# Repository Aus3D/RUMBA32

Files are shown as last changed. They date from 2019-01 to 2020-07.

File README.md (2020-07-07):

# RUMBA32




RUMBA32 is a 32-bit version of the RUMBA 3D Printer control board. RUMBA32 is derived from the Aus3D [RUMBA+](https://github.com/Aus3D/RUMBA-Plus) design, which is an overhauled version of the original RUMBA.

RUMBA32 combines the improved RUMBA+ design with a powerful 32-bit STM32F446 microcontroller.

In keeping with the original RUMBA design, RUMBA32 is fully open source. RUMBA32 boards are available for sale in the [Aus3D shop](https://aus3d.com.au/rumba32). 

Instructions for configuring and uploading Marlin using PlatformIO can be found on the [Marlin - Build and Upload (PlatformIO)](https://github.com/Aus3D/RUMBA32/wiki/Marlin---Build-and-Upload-(PlatformIO)) wiki page.

## Firmware Support
RUMBA32 is currently supported by the following firmware:
- [MK4duo (support in v4.4.0)](https://github.com/MKFirmware/MK4duo)
- [Marlin 2.0 (support in bugfix-2.0.x)](https://github.com/MarlinFirmware/Marlin)
- [Repetier-Firmware V2 (support in dev2)](https://github.com/repetier/Repetier-Firmware/tree/dev2)

## Images
### Overview
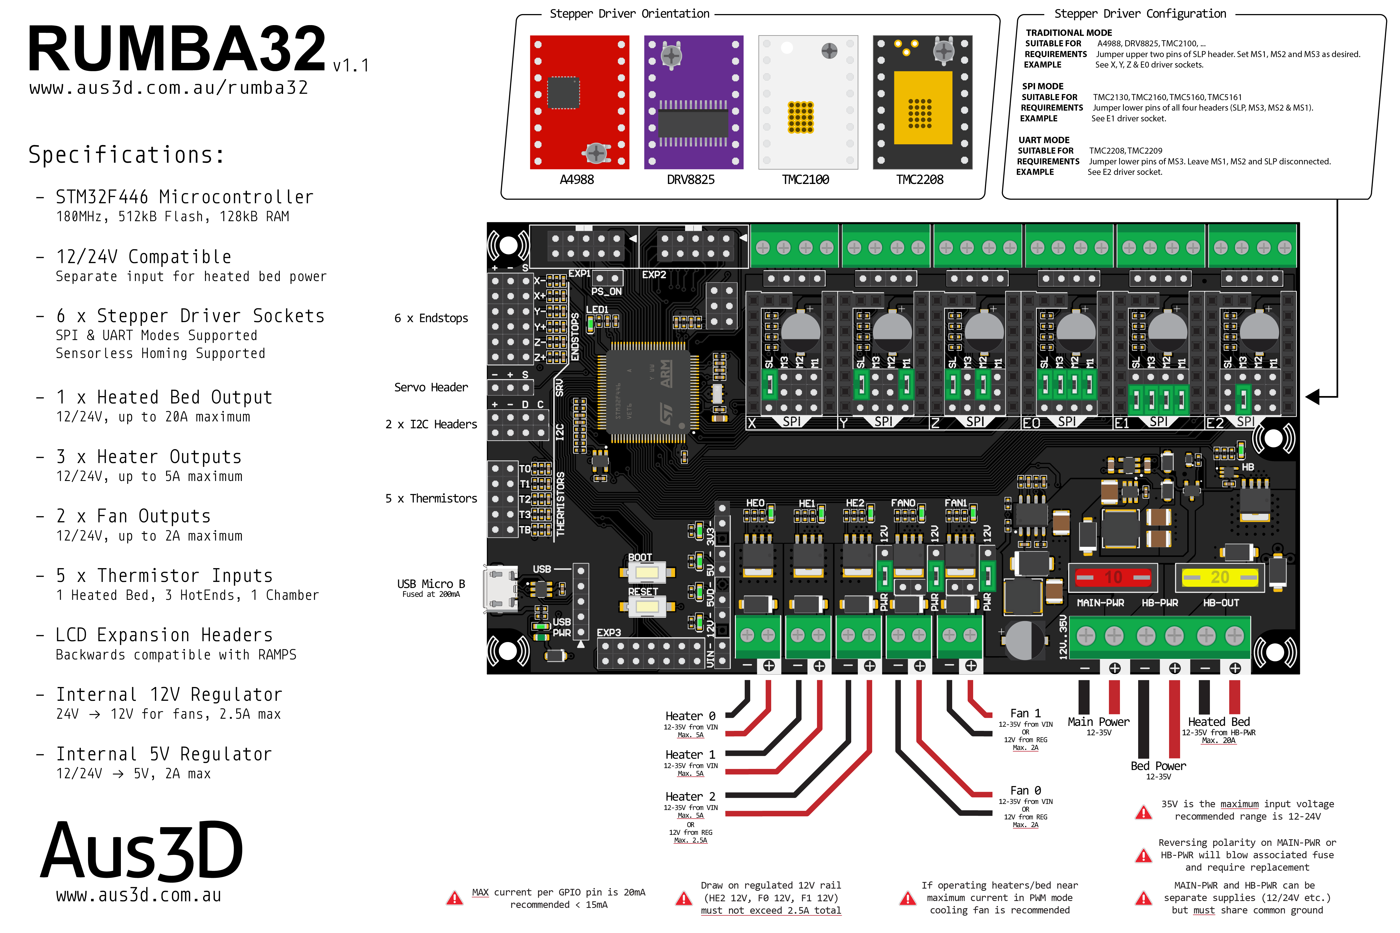
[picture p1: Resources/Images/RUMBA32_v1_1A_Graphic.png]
RUMBA32 Graphic

### Photo
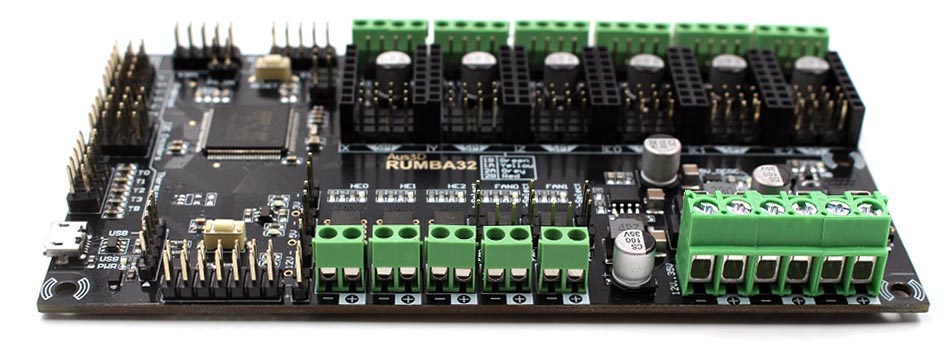
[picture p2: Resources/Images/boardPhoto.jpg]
RUMBA32 Photo

### Schematic
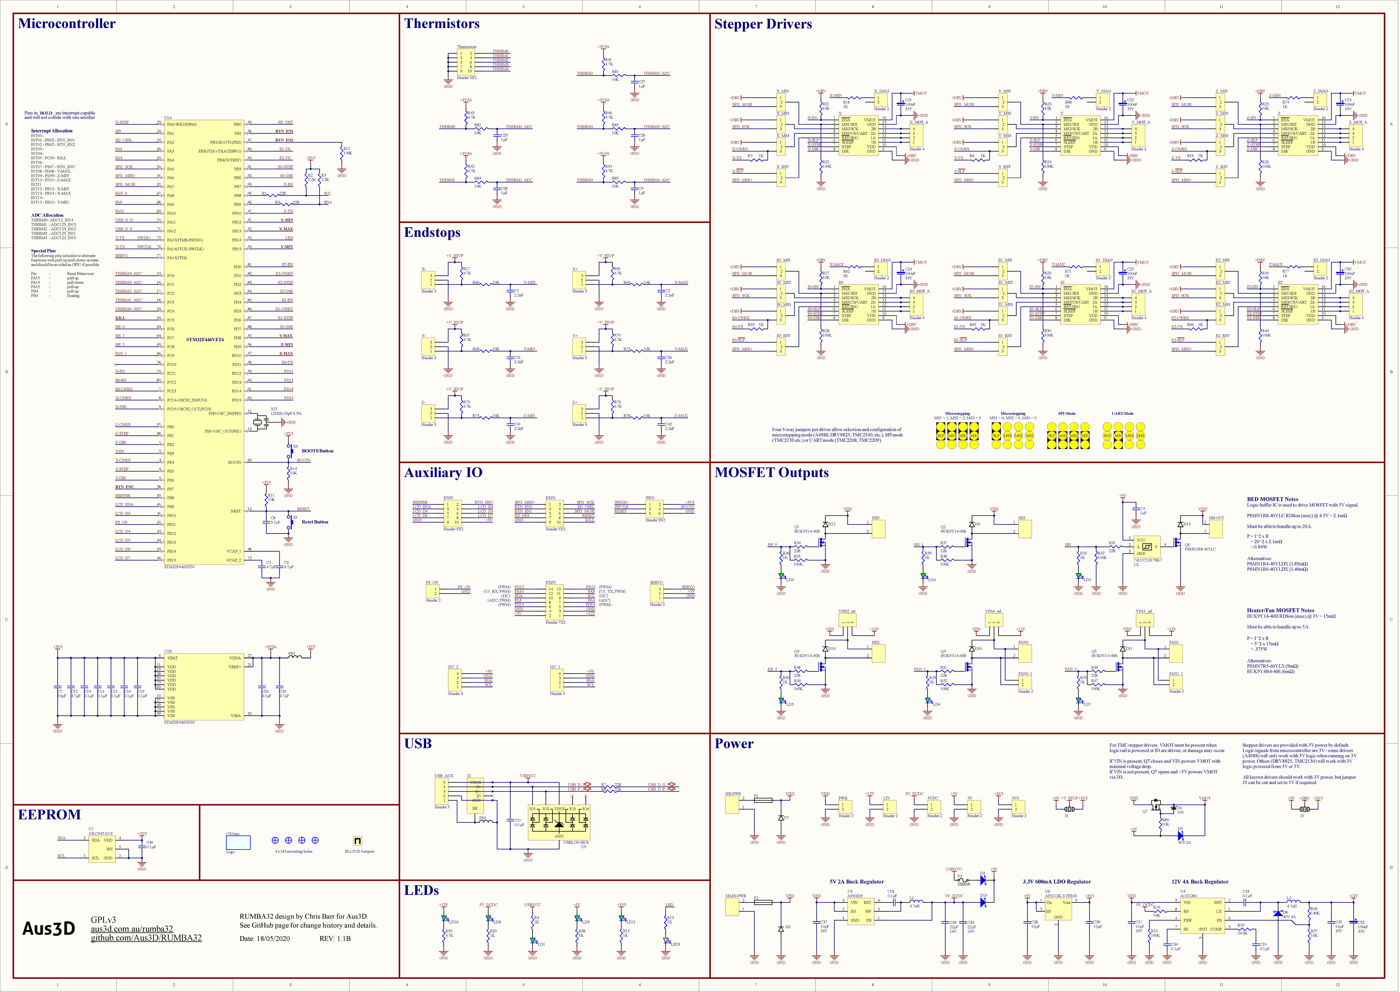
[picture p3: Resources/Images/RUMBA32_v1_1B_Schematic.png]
RUMBA32 Schematic

### Pinout
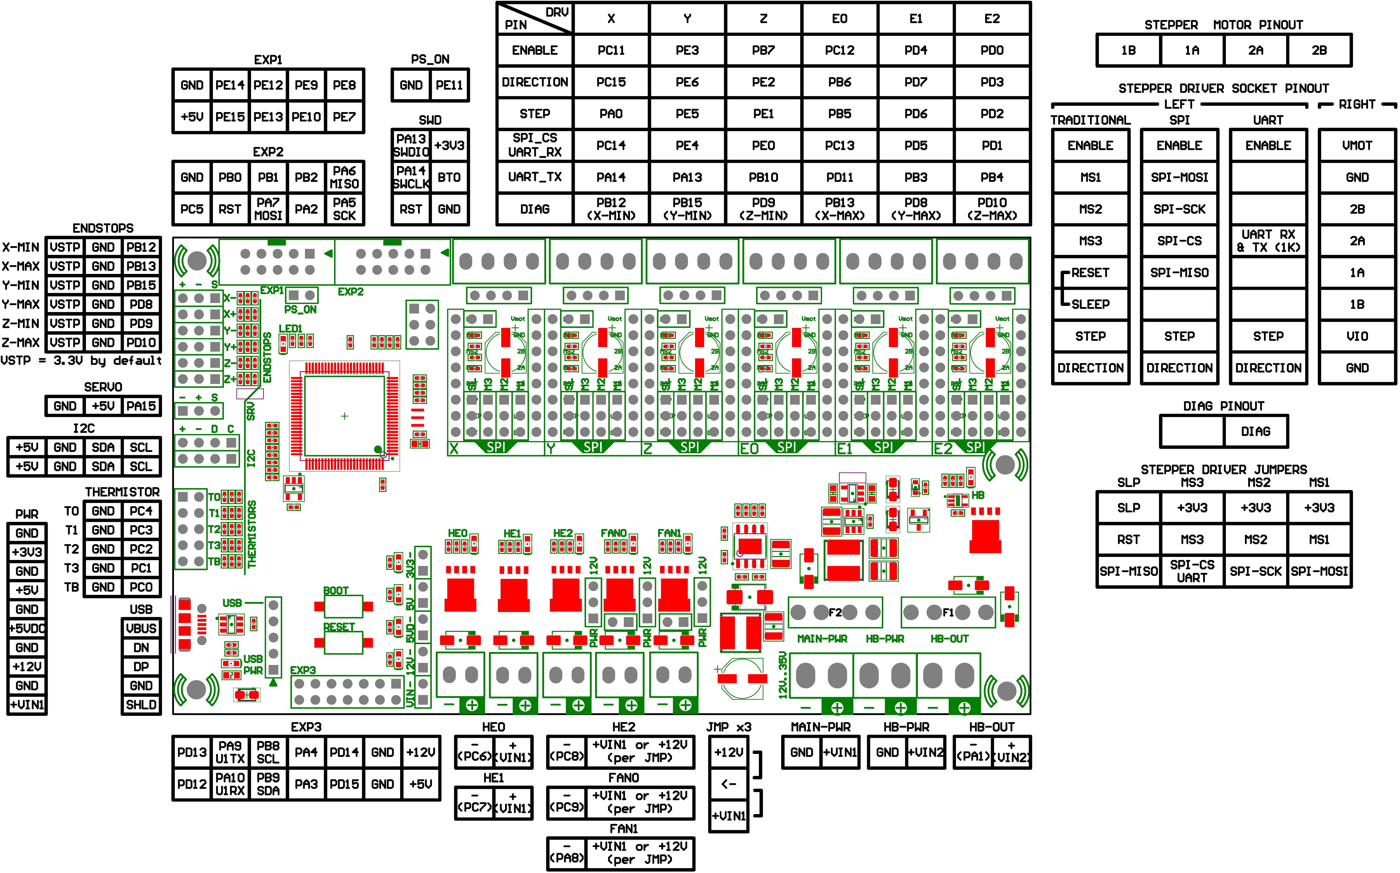
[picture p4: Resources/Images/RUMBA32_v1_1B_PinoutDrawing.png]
RUMBA32 Pinout

### Dimensions
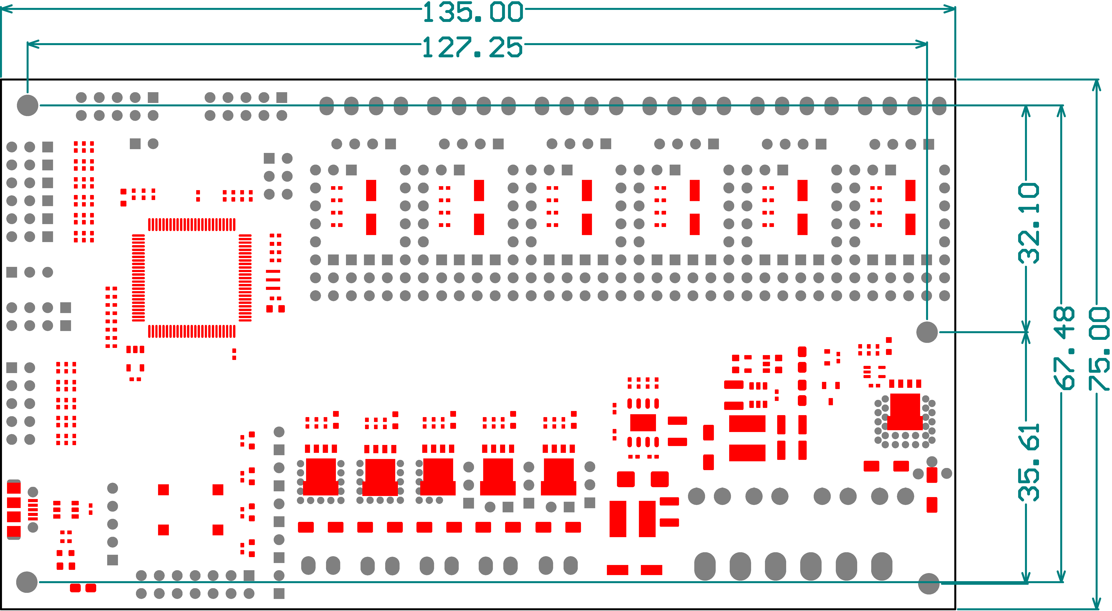
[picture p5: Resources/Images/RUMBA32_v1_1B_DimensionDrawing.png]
RUMBA32 Dimensions


## License
RUMBA32 is fully open source, and may be freely modified or changed by anyone, provided they maintain the license it is released under. The design is free to use for any purpose, including commercial uses. RUMBA32 maintains the GPLv2 license of the original RUMBA board. For more information on this license, please see the included license file.

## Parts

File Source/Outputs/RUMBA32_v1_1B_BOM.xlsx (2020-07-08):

Designator | Description | Quantity | Note | Manufacturer 1 | Manufacturer Part Number 1 | Supplier 1 | Supplier Part Number 1
JMP, JMP1 | 2.54mm .1" PCB Jumper, Green | 28 | Installed as per drawing, approved sub OK | Sullins | QPC02SXGN-RC | Digi-Key | S9337-ND
C21, C22, C23, C24, C25, C30, C32 | CAP ALUM 100UF 20% 35V SMD | 7 | Approved sub OK | Panasonic | EEEFT1V101AP | Digi-Key | PCE5016CT-ND
C8, C10, C11, C13, C14, C15, C16, C18, C19, C20, C33, C34, C40 | CAP CER 0.1UF 50V X7R 0402 | 13 | Approved sub OK | Taiyo Yuden | UMK105B7104KV-FR | Digi-Key | 587-3498-1-ND
C4, C9, C26, C27, C28, C29 | CAP CER 1UF 16V X5R 0402 | 6 | Approved sub OK | Taiyo | EMK105BJ105KV-F | Digi-Key | 587-2477-1-ND
C1, C2, C31, C36, C41, C42 | CAP CER 2.2NF 50V X7R 0402 | 6 | Approved sub OK | Taiyo Yuden | RMUMK105B7222KV-F | Digi-Key | 587-1221-1-ND
C5, C6, C12, C35 | CAP CER 4.7UF 10V X5R 0402 | 4 | Approved sub OK | Taiyo Yuden | LMK105BBJ475MVLF | Digi-Key | 587-3408-1-ND
C7, C38, C39 | CAP CER 10UF 10V X5R 0603 | 3 | Approved sub OK | Taiyo Yuden | LMK107BBJ106KALT | Digi-Key | 587-6017-1-ND
C17, C37, C45 | CAP CER 10UF 35V X7R 1210 | 3 | Approved sub OK | Taiyo Yuden | GMJ325KB7106KMHP | Digi-Key | 587-4890-1-ND
C43, C44 | CAP CER 22UF 16V X7R 1210 | 2 | Approved sub OK | Taiyo Yuden | EMJ325KB7226KMHP | Digi-Key | 587-5657-1-ND
XT1 | CER RES 12.0000MHZ 33PF SMD | 1 | Approved sub OK | Murata | CSTNE12M0G550000R0 | Digi-Key | 490-17943-1-ND
J2 | CONN RCPT USB2.0 MICRO B SMD R/A | 1 | Approved sub OK | Molex | 105017-0001 | Digi-Key | WM1399CT-ND
D6, D7, D9, D10, D11, D12, D13, D14 | DIODE GEN PURP 100V 1.5A SMA | 8 | Approved sub OK | Diodes | S2BA-13-F | Digi-Key | S2BA-FDICT-ND
D3, D4, D15 | DIODE SCHOTTKY 40V 2A SOD123F | 3 | Approved sub OK | ON Semiconductor / Fairchild | SS24FL | Digi-Key | SS24FLCT-ND
D8 | DIODE SCHOTTKY 40V 4A DO214AA | 1 | Approved sub OK | Vishay Semiconductors | SSB44-E3/52T | Digi-Key | SSB44-E3/52TGICT-ND
U5 | DIODE TVS 5.25V 17V SOT23-6 | 1 | Approved sub OK | STMicroelectronics | USBLC6-4SC6 | Digi-Key | 497-4492-1-ND
D1 | DIODE ZENER 10V 500mW SOD523 | 1 | Approved sub OK | ON Semiconductor | MM5Z10VT1G | Digi-Key | MM5Z10VT1GOSCT-ND
FB1, FB2 | FERRITE BEAD 120R 300MA 0402 | 2 | Approved sub OK | Taiyo Yuden | BK1005HM121-T | Digi-Key | 587-1836-1-ND
L1, L2 | FIXED IND 4.7UH 4.5A 26 MOHM SMD | 2 | Approved sub OK | Bourns | SRN6045TA-4R7M | Digi-Key | SRN6045TA-4R7MCT-ND
F1, F2 | FUSE HOLDER BLADE PCB | 2 | Approved sub OK | Memory Protection Devices | BK-6013 | Digi-Key | BK-6013-ND
3V3, 5V, 5VDC, 12V, FAN0_1, FAN1_1, PS_ON, PWR | Header, 2-Pin | 8 | Approved sub OK | Generic Header
E0_DIAG, E1_DIAG, E2_DIAG, X_DIAG, Y_DIAG, Z_DIAG | Header, 2-Pin, Female | 6 | Approved sub OK | Generic Header
E0_MS1, E0_MS2, E0_MS3, E0_RST, E1_MS1, E1_MS2, E1_MS3, E1_RST, E2_MS1, E2_MS2, E2_MS3, E2_RST, SERVO, VFA0_sel, VFA1_sel, VHE2_sel, X-, X_MS1, X_MS2, X_MS3, X_RST, X+, Y-, Y_MS1, Y_MS2, Y_MS3, Y_RST, Y+, Z-, Z_MS1, Z_MS2, Z_MS3, Z_RST, Z+ | Header, 3-Pin | 34 | Approved sub OK | Generic Header
SWD | Header, 3-Pin, Dual row | 1 | Approved sub OK | Generic Header
E0_MOT_A, E1_MOT_A, E2_MOT_A, I2C_1, I2C_2, X_MOT_A, Y_MOT_A, Z_MOT_A | Header, 4-Pin | 8 | Approved sub OK | Generic Header
USB_AUX | Header, 5-Pin | 1 | Approved sub OK | Generic Header
EXP1, EXP2, Thermistors | Header, 5-Pin, Dual row | 3 | Approved sub OK | Generic Header
EXP3 | Header, 7-Pin, Dual row | 1 | Approved sub OK | Generic Header
E0_0, E0_1, E1_0, E1_1, E2_0, E2_1, X_0, X_1, Y_0, Y_1, Z_0, Z_1 | Header, 8-Pin, Female | 12 | Approved sub OK | Generic Header
U2 | IC BUF NON-INVERT 5.5V SOT353 | 1 |  | Diodes | 74LVC1G17SE-7 | Digi-Key | 74LVC1G17SE-7CT-ND
U7 | IC EEPROM 64K I2C SOT23-5 | 1 |  | Microchip | 24LC64T-I/OT | Digi-Key | 24LC64T-I/OTCT-ND
U1 | IC MCU 32BIT 512KB FLASH 100LQFP | 1 |  | STMicroelectronics | STM32F446VET6 | Digi-Key | 497-15375-ND
U3 | IC REG BUCK 5V 2A SOT23-6 | 1 |  | Diodes | AP63205WU-7 | Digi-Key | AP63205WU-7DICT-ND
U4 | IC REG BUCK ADJ 4A 8SO | 1 |  | Alpha & Omega Semiconductor | AOZ1284PI | Digi-Key | 785-1689-1-ND
U6 | IC REG LINEAR 3.3V 600MA SOT25 | 1 |  | Diodes | AP2112K-3.3TRG1 | Digi-Key | AP2112K-3.3TRG1DICT-ND
LD1, LD2, LD3, LD4, LD5, LD6, LD7, LD8, LD9, LD10, LD11 | LED GREEN CLEAR CHIP SMD 0603 | 11 | Approved sub OK | Vishay Lite-On | LTST-C190KGKT | Digi-Key | 160-1435-2-ND
LED1 | LED YELLOW CLEAR CHIP SMD 0603 | 1 | Approved sub OK | Vishay Lite-On | LTST-C190KSKT | Digi-Key | 160-1437-1-ND
Q1, Q2, Q3, Q4, Q5 | MOSFET N-CH 40V 56A LFPAK | 5 |  | Nexperia USA | BUK9Y14-40B,115 | Digi-Key | 1727-4940-1-ND
Q6 | MOSFET N-CH 40V 100A LFPAK | 1 |  | Nexperia | PSMN1R8-40YLC,115 | Digi-Key | 1727-1052-1-ND
Q7 | MOSFET SMD P-CH 30V 4.8A SOT-23-3 | 1 |  | Vishay Siliconix | SI2371EDS-T1-GE3 | Digi-Key | SI2371EDS-T1-GE3CT-ND
F3 | PTC RESET FUSE 9V 200MA 0603 | 1 | Approved sub OK | BEL FUSE - CIRCUIT PROTECTION | 0ZCM0020FF2G | Digi-Key | 507-1821-1-ND
R4, R5, R6, R13, R15, R16, R18, R20, R33, R36, R39, R50, R53, R55, R58, R62, R64, R65, R66, R68, R71, R74, R77 | RES SMD 1K OHM 1% 1/16W 0402 | 23 | Approved sub OK | Yageo | RC0402FR-071KL | Digi-Key | 311-1.00KLRCT-ND
R2, R3 | RES SMD 2.2K OHM 1% 1/16W 0402 | 2 | Approved sub OK | Yageo | RC0402FR-072K2L | Digi-Key | 311-2.20KLRCT-ND
R17, R40, R41, R42, R43, R54, R59, R61, R67, R70, R73, R76 | RES SMD 4.7K OHM 1% 1/16W 0402 | 12 | Approved sub OK | Yageo | RC0402FR-074K7L | Digi-Key | 311-4.7KLRCT-ND
R11, R14, R21, R23, R25, R27, R29, R45, R57, R60, R63, R69, R72, R75, R78, R79, R80, R81, R82, R83, R84, R85 | RES SMD 10K OHM 1% 1/16W 0402 | 22 | Approved sub OK | Yageo | RC0402FR-0710KL | Digi-Key | 311-10.0KLRCT-ND
R1, R7, R8, R9, R31, R34, R37, R46, R48, R51 | RES SMD 22 OHM 1% 1/16W 0402 | 10 | Approved sub OK | Yageo | RC0402FR-0722RL | Digi-Key | 311-22.0LRCT-ND
R19 | RES SMD 54.9K OHM 1% 1/16W 0402 | 1 | Approved sub OK | Yageo | RC0402FR-0754K9L | Digi-Key | YAG3185CT-ND
R10, R12, R22, R24, R26, R28, R30, R32, R35, R38, R44, R47, R49, R52 | RES SMD 100K OHM 1% 1/16W 0402 | 14 | Approved sub OK | Yageo | RC0402FR-07100KL | Digi-Key | 311-100KLRCT-ND
R56 | RES SMD 140K OHM 1% 1/16W 0402 | 1 | Approved sub OK | Yageo | RC0402FR-07140KL | Digi-Key | YAG2978CT-ND
S1, S3 | SWITCH TACTILE SPST-NO 0.05A 12V | 2 | Approved sub OK | APEM | MJTP1106SATR | Digi-Key | 679-2396-1-ND
FAN0, FAN1, HE0, HE1, HE2 | TERM BLK 2POS SIDE ENT 3.5MM PCB | 5 | Approved sub OK | Phoenix Contact | 1751248 | Digi-Key | 277-5719-ND
HB-OUT, HB-PWR, MAIN-PWR | TERM BLK 2POS SIDE ENTRY 5MM PCB | 3 |  | Phoenix Contact | 1935776 | Digi-Key | 277-6405-ND
E0_MOT, E1_MOT, E2_MOT, X_MOT, Y_MOT, Z_MOT | TERM BLK 4POS SIDE ENT 3.5MM PCB | 6 | Approved sub OK | Phoenix Contact | 1751264 | Digi-Key | 277-5744-ND

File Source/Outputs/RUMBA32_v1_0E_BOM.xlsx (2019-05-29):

Designator | Description | Quantity | Note | Manufacturer 1 | Manufacturer Part Number 1 | Supplier 1 | Supplier Part Number 1
JMP | 2.54mm .1" PCB Jumper, Green | 27 | Installed as per drawing, approved sub OK | Sullins (https://octopart-clicks.com/click/altium?sku=S9337-ND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) | QPC02SXGN-RC (https://octopart-clicks.com/click/altium?sku=S9337-ND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) | Digi-Key | S9337-ND (https://octopart-clicks.com/click/altium?sku=S9337-ND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)
C1, C21, C22, C23, C24, C25, C30, C31, C32 | CAP ALUM 100UF 20% 35V SMD | 9 | Approved sub OK | Panasonic (https://octopart-clicks.com/click/altium?sku=PCE5016CT-ND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) | EEEFT1V101AP (https://octopart-clicks.com/click/altium?sku=PCE5016CT-ND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) | Digi-Key | PCE5016CT-ND (https://octopart-clicks.com/click/altium?sku=PCE5016CT-ND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)
C3, C8, C10, C11, C13, C14, C15, C16, C18, C19, C20, C33, C34 | CAP CER 0.1UF 50V X7R 0603 | 13 | Approved sub OK | Yageo (https://octopart-clicks.com/click/altium?sku=311-1344-1-ND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) | CC0603KRX7R9BB104 (https://octopart-clicks.com/click/altium?sku=311-1344-1-ND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) | Digi-Key | 311-1344-1-ND (https://octopart-clicks.com/click/altium?sku=311-1344-1-ND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)
C4, C9, C26, C27, C28, C29 | CAP CER 1UF 16V X7R 0603 | 6 | Approved sub OK | Taiyo Yuden (https://octopart-clicks.com/click/altium?sku=587-1241-1-ND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) | EMK107B7105KA-T (https://octopart-clicks.com/click/altium?sku=587-1241-1-ND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) | Digi-Key | 587-1241-1-ND (https://octopart-clicks.com/click/altium?sku=587-1241-1-ND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)
C2, C5, C6, C12, C35, C38, C39 | CAP CER 4.7UF 10V X7R 0603 | 7 | Approved sub OK | TDK (https://octopart-clicks.com/click/altium?sku=445-1604-1-ND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) | C1608X7R1C105K080AC (https://octopart-clicks.com/click/altium?sku=445-1604-1-ND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) | Digi-Key | 445-1604-1-ND (https://octopart-clicks.com/click/altium?sku=445-1604-1-ND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)
C17, C36, C37 | CAP CER 4.7UF 50V X7R 1210 | 3 | Approved sub OK | KEMET (https://octopart-clicks.com/click/altium?sku=399-6785-1-ND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) | C1210C475K5RACTU (https://octopart-clicks.com/click/altium?sku=399-6785-1-ND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) | Digi-Key | 399-6785-1-ND (https://octopart-clicks.com/click/altium?sku=399-6785-1-ND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)
C7 | CAP CER 10UF 6.3V X7R 0805 | 1 | Approved sub OK | Samsung (https://octopart-clicks.com/click/altium?sku=1276-1113-1-ND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) | CL21B106KQQNNNE (https://octopart-clicks.com/click/altium?sku=1276-1113-1-ND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) | Digi-Key | 1276-1113-1-ND (https://octopart-clicks.com/click/altium?sku=1276-1113-1-ND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)
XT1 | CER RES 12.0000MHZ 33PF SMD | 1 | Approved sub OK | Murata (https://octopart-clicks.com/click/altium?sku=490-17943-1-ND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) | CSTNE12M0G550000R0 (https://octopart-clicks.com/click/altium?sku=490-17943-1-ND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) | Digi-Key | 490-17943-1-ND (https://octopart-clicks.com/click/altium?sku=490-17943-1-ND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)
J2 | CONN RCPT USB2.0 MICRO B SMD R/A | 1 | Approved sub OK | Molex (https://octopart-clicks.com/click/altium?sku=WM1399CT-ND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) | 105017-0001 (https://octopart-clicks.com/click/altium?sku=WM1399CT-ND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) | Digi-Key | WM1399CT-ND (https://octopart-clicks.com/click/altium?sku=WM1399CT-ND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)
D6, D7, D9, D10, D11, D12, D13, D14 | DIODE GEN PURP 100V 1.5A SMA | 8 | Approved sub OK | Diodes (https://octopart-clicks.com/click/altium?sku=S2BA-FDICT-ND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) | S2BA-13-F (https://octopart-clicks.com/click/altium?sku=S2BA-FDICT-ND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) | Digi-Key | S2BA-FDICT-ND (https://octopart-clicks.com/click/altium?sku=S2BA-FDICT-ND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)
D3, D4, D5, D15 | DIODE SCHOTTKY 40V 2A SOD123F | 4 | Approved sub OK | ON Semiconductor / Fairchild (https://octopart-clicks.com/click/altium?manufacturer=ON%20Semiconductor%20%2F%20Fairchild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) | SS24FL (https://octopart-clicks.com/click/altium?manufacturer=ON%20Semiconductor%20%2F%20Fairchild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) | Digi-Key | SS24FLCT-ND (https://octopart-clicks.com/click/altium?manufacturer=ON%20Semiconductor%20%2F%20Fairchild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)
D2, D8 | DIODE SCHOTTKY 40V 4A DO214AA | 2 | Approved sub OK | General Instruments (https://octopart-clicks.com/click/altium?manufacturer=General%20Instruments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) | SSB44-E3/52T (https://octopart-clicks.com/click/altium?manufacturer=General%20Instruments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) | Digi-Key | SSB44-E3/52TGICT-ND (https://octopart-clicks.com/click/altium?manufacturer=General%20Instruments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)
FB1, FB2 | FERRITE BEAD 120 OHM 0603 1LN | 2 | Approved sub OK | Murata (https://octopart-clicks.com/click/altium?sku=490-1037-1-ND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) | BLM18PG-121SN1D (https://octopart-clicks.com/click/altium?sku=490-1037-1-ND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) | Digi-Key | 490-1037-1-ND (https://octopart-clicks.com/click/altium?sku=490-1037-1-ND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)
L2 | FIXED IND 4.7UH 4.5A 26 MOHM SMD | 1 | Approved sub OK | Bourns (https://octopart-clicks.com/click/altium?sku=SRN6045TA-4R7MCT-ND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) | SRN6045TA-4R7M (https://octopart-clicks.com/click/altium?sku=SRN6045TA-4R7MCT-ND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) | Digi-Key | SRN6045TA-4R7MCT-ND (https://octopart-clicks.com/click/altium?sku=SRN6045TA-4R7MCT-ND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)
L1 | FIXED IND 33UH 1.8A 145 MOHM SMD | 1 | Approved sub OK | Bourns (https://octopart-clicks.com/click/altium?sku=SRN6045TA-330MCT-ND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) | SRN6045TA-330M (https://octopart-clicks.com/click/altium?sku=SRN6045TA-330MCT-ND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) | Digi-Key | SRN6045TA-330MCT-ND (https://octopart-clicks.com/click/altium?sku=SRN6045TA-330MCT-ND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)
F1, F2 | FUSE HOLDER BLADE PCB | 2 | Approved sub OK | Memory Protection Devices (https://octopart-clicks.com/click/altium?sku=BK-6013-ND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) | BK-6013 (https://octopart-clicks.com/click/altium?sku=BK-6013-ND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) | Digi-Key | BK-6013-ND (https://octopart-clicks.com/click/altium?sku=BK-6013-ND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)
3V3, 5V, 12V, FAN0_1, FAN1_1, PS_ON, PWR | Header, 2-Pin | 7 | Approved sub OK | Generic Header
E0_MS1, E0_MS2, E0_MS3, E0_SLP, E1_MS1, E1_MS2, E1_MS3, E1_SLP, E2_MS1, E2_MS2, E2_MS3, E2_SLP, VFA0_sel, VFA1_sel, VHE2_sel, X-, X_MS1, X_MS2, X_MS3, X_SLP, X+, Y-, Y_MS1, Y_MS2, Y_MS3, Y_SLP, Y+, Z-, Z_MS1, Z_MS2, Z_MS3, Z_SLP, Z+ | Header, 3-Pin | 33 | Approved sub OK | Generic Header
ISP1 | Header, 3-Pin, Dual row | 1 | Approved sub OK | Generic Header
E0_MOT_A, E1_MOT_A, E2_MOT_A, ENC_1, ENC_2, ENC_3, ENC_4, X_MOT_A, Y_MOT_A, Z_MOT_A | Header, 4-Pin | 10 | Approved sub OK | Generic Header
USB_AUX | Header, 5-Pin | 1 | Approved sub OK | Generic Header
EXP1, EXP2, Thermistors | Header, 5-Pin, Dual row | 3 | Approved sub OK | Generic Header
EXP3 | Header, 7-Pin, Dual row | 1 | Approved sub OK | Generic Header
E0_0, E0_1, E1_0, E1_1, E2_0, E2_1, X_0, X_1, Y_0, Y_1, Z_0, Z_1 | Header, 8-Pin, Female | 12 | Approved sub OK | Generic Header
U2 | IC BUF NON-INVERT 5.5V SOT353 | 1 |  | Diodes (https://octopart-clicks.com/click/altium?sku=74LVC1G17SE-7CT-ND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) | 74LVC1G17SE-7 (https://octopart-clicks.com/click/altium?sku=74LVC1G17SE-7CT-ND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) | Digi-Key | 74LVC1G17SE-7CT-ND (https://octopart-clicks.com/click/altium?sku=74LVC1G17SE-7CT-ND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)
U1 | IC MCU 32BIT 512KB FLASH 100LQFP | 1 |  | STMicroelectronics (https://octopart-clicks.com/click/altium?sku=497-15375-ND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) | STM32F446VET6 (https://octopart-clicks.com/click/altium?sku=497-15375-ND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) | Digi-Key | 497-15375-ND (https://octopart-clicks.com/click/altium?sku=497-15375-ND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)
U3 | IC REG BUCK ADJ 1.2A SOT23-6 | 1 |  | Alpha & Omega Semiconductor (https://octopart-clicks.com/click/altium?manufacturer=Alpha%20%26%20Omega%20Semiconductor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) | AOZ1282CI (https://octopart-clicks.com/click/altium?manufacturer=Alpha%20%26%20Omega%20Semiconductor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) | Digi-Key | 785-1613-1-ND (https://octopart-clicks.com/click/altium?manufacturer=Alpha%20%26%20Omega%20Semiconductor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)
U4 | IC REG BUCK ADJ 4A 8SO | 1 |  | Alpha & Omega Semiconductor (https://octopart-clicks.com/click/altium?manufacturer=Alpha%20%26%20Omega%20Semiconductor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) | AOZ1284PI (https://octopart-clicks.com/click/altium?manufacturer=Alpha%20%26%20Omega%20Semiconductor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) | Digi-Key | 785-1689-1-ND (https://octopart-clicks.com/click/altium?manufacturer=Alpha%20%26%20Omega%20Semiconductor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)
U6 | IC REG LINEAR 3.3V 600MA SOT25 | 1 |  | Diodes (https://octopart-clicks.com/click/altium?sku=AP2112K-3.3TRG1DICT-ND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) | AP2112K-3.3TRG1 (https://octopart-clicks.com/click/altium?sku=AP2112K-3.3TRG1DICT-ND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) | Digi-Key | AP2112K-3.3TRG1DICT-ND (https://octopart-clicks.com/click/altium?sku=AP2112K-3.3TRG1DICT-ND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)
LD1, LD2, LD3, LD4, LD5, LD6, LD7, LD8, LD9, LD10, LD11 | LED GREEN CLEAR CHIP SMD 0603 | 11 | Approved sub OK | Vishay Lite-On (https://octopart-clicks.com/click/altium?sku=160-1435-2-ND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) | LTST-C190KGKT (https://octopart-clicks.com/click/altium?sku=160-1435-2-ND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) | Digi-Key | 160-1435-2-ND (https://octopart-clicks.com/click/altium?sku=160-1435-2-ND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)
LED1 | LED YELLOW CLEAR CHIP SMD 0603 | 1 | Approved sub OK | Vishay Lite-On (https://octopart-clicks.com/click/altium?sku=160-1437-1-ND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) | LTST-C190KSKT (https://octopart-clicks.com/click/altium?sku=160-1437-1-ND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) | Digi-Key | 160-1437-1-ND (https://octopart-clicks.com/click/altium?sku=160-1437-1-ND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)
Q1, Q2, Q3, Q4, Q5 | MOSFET N-CH 40V 56A LFPAK | 5 |  | Nexperia USA (https://octopart-clicks.com/click/altium?sku=1727-4940-1-ND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) | BUK9Y14-40B,115 (https://octopart-clicks.com/click/altium?sku=1727-4940-1-ND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) | Digi-Key | 1727-4940-1-ND (https://octopart-clicks.com/click/altium?sku=1727-4940-1-ND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)
Q6 | MOSFET N-CH 40V 100A LFPAK | 1 |  | Nexperia (https://octopart-clicks.com/click/altium?sku=1727-1052-1-ND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) | PSMN1R8-40YLC,115 (https://octopart-clicks.com/click/altium?sku=1727-1052-1-ND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) | Digi-Key | 1727-1052-1-ND (https://octopart-clicks.com/click/altium?sku=1727-1052-1-ND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)
F3 | PTC RESET FUSE 9V 200MA 0603 | 1 | Approved sub OK | Bel (https://octopart-clicks.com/click/altium?sku=507-1821-1-ND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) | 0ZCM0020FF2G (https://octopart-clicks.com/click/altium?sku=507-1821-1-ND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) | Digi-Key | 507-1821-1-ND (https://octopart-clicks.com/click/altium?sku=507-1821-1-ND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)
R4, R13, R15, R20, R33, R36, R39, R50, R53, R55, R58 | RES SMD 1K OHM 1% 1/10W 0603 | 11 | Approved sub OK | Yageo (https://octopart-clicks.com/click/altium?sku=311-1.00KHRCT-ND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) | RC0603FR-071KL (https://octopart-clicks.com/click/altium?sku=311-1.00KHRCT-ND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) | Digi-Key | 311-1.00KHRCT-ND (https://octopart-clicks.com/click/altium?sku=311-1.00KHRCT-ND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)
R2, R3 | RES SMD 2.2K OHM 1% 1/10W 0603 | 2 | Approved sub OK | Yageo (https://octopart-clicks.com/click/altium?sku=311-2.20KHRCT-ND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) | RC0603FR-072K2L (https://octopart-clicks.com/click/altium?sku=311-2.20KHRCT-ND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) | Digi-Key | 311-2.20KHRCT-ND (https://octopart-clicks.com/click/altium?sku=311-2.20KHRCT-ND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)
R40, R41, R42, R43, R54, R59 | RES SMD 4.7K OHM 1% 1/10W 0603 | 6 | Approved sub OK | Yageo (https://octopart-clicks.com/click/altium?sku=311-4.70KHRCT-ND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) | RC0603FR-074K7L (https://octopart-clicks.com/click/altium?sku=311-4.70KHRCT-ND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) | Digi-Key | 311-4.70KHRCT-ND (https://octopart-clicks.com/click/altium?sku=311-4.70KHRCT-ND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)
R6, R11, R12, R14, R21, R23, R25, R27, R29, R45, R57 | RES SMD 10K OHM 1% 1/10W 0603 | 11 | Approved sub OK | Yageo Phycomp (https://octopart-clicks.com/click/altium?sku=311-10.0KHRCT-ND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) | RC0603FR-0710KL (https://octopart-clicks.com/click/altium?sku=311-10.0KHRCT-ND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) | Digi-Key | 311-10.0KHRCT-ND (https://octopart-clicks.com/click/altium?sku=311-10.0KHRCT-ND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)
R1, R7, R8, R9, R31, R34, R37, R46, R48, R51 | RES SMD 22 OHM 1% 1/10W 0603 | 10 | Approved sub OK | Yageo (https://octopart-clicks.com/click/altium?sku=311-22.0HRCT-ND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) | RC0603FR-0722RL (https://octopart-clicks.com/click/altium?sku=311-22.0HRCT-ND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) | Digi-Key | 311-22.0HRCT-ND (https://octopart-clicks.com/click/altium?sku=311-22.0HRCT-ND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)
R5, R19 | RES SMD 54.9K OHM 1% 1/10W 0603 | 2 | Approved sub OK | Yageo (https://octopart-clicks.com/click/altium?sku=311-54.9KHRCT-ND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) | RC0603FR-0754K9L (https://octopart-clicks.com/click/altium?sku=311-54.9KHRCT-ND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) | Digi-Key | 311-54.9KHRCT-ND (https://octopart-clicks.com/click/altium?sku=311-54.9KHRCT-ND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)
R10, R22, R24, R26, R28, R30, R32, R35, R38, R44, R47, R49, R52 | RES SMD 100K OHM 1% 1/10W 0603 | 13 | Approved sub OK | Yageo (https://octopart-clicks.com/click/altium?sku=311-100KHRCT-ND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) | RC0603FR-07100KL (https://octopart-clicks.com/click/altium?sku=311-100KHRCT-ND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) | Digi-Key | 311-100KHRCT-ND (https://octopart-clicks.com/click/altium?sku=311-100KHRCT-ND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)
R56 | RES SMD 140K OHM 1% 1/10W 0603 | 1 | Approved sub OK | Yageo (https://octopart-clicks.com/click/altium?sku=311-140KHRCT-ND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) | RC0603FR-07140KL (https://octopart-clicks.com/click/altium?sku=311-140KHRCT-ND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) | Digi-Key | 311-140KHRCT-ND (https://octopart-clicks.com/click/altium?sku=311-140KHRCT-ND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)
S1, S2, S3 | SWITCH TACTILE SPST-NO 0.05A 12V | 3 | Approved sub OK | APEM (https://octopart-clicks.com/click/altium?sku=679-2396-1-ND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) | MJTP1106SATR (https://octopart-clicks.com/click/altium?sku=679-2396-1-ND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) | Digi-Key | 679-2396-1-ND (https://octopart-clicks.com/click/altium?sku=679-2396-1-ND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)
FAN0, FAN1, HE0, HE1, HE2 | TERM BLK 2POS SIDE ENT 3.5MM PCB | 5 | Approved sub OK | Phoenix Contact (https://octopart-clicks.com/click/altium?sku=277-5719-ND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) | MKDS1/2-3,5 (https://octopart-clicks.com/click/altium?sku=277-5719-ND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) | Digi-Key | 277-5719-ND (https://octopart-clicks.com/click/altium?sku=277-5719-ND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)
HB-OUT, HB-PWR, MAIN-PWR | TERM BLK 2POS SIDE ENTRY 5MM PCB | 3 |  | Phoenix Contact (https://octopart-clicks.com/click/altium?sku=277-6405-ND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) | 1935776 (https://octopart-clicks.com/click/altium?sku=277-6405-ND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) | Digi-Key | 277-6405-ND (https://octopart-clicks.com/click/altium?sku=277-6405-ND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)
E0_MOT, E1_MOT, E2_MOT, X_MOT, Y_MOT, Z_MOT | TERM BLK 4POS SIDE ENT 3.5MM PCB | 6 | Approved sub OK | Phoenix Contact (https://octopart-clicks.com/click/altium?sku=277-5744-ND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) | MKDS1/4-3,5 (https://octopart-clicks.com/click/altium?sku=277-5744-ND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) | Digi-Key | 277-5744-ND (https://octopart-clicks.com/click/altium?sku=277-5744-ND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)
U5 | TVS DIODE 5.25V 17V SOT23-6 | 1 | Approved sub OK | STMicroelectronics (https://octopart-clicks.com/click/altium?sku=497-4492-1-ND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) | USBLC6-4SC6 (https://octopart-clicks.com/click/altium?sku=497-4492-1-ND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) | Digi-Key | 497-4492-1-ND (https://octopart-clicks.com/click/altium?sku=497-4492-1-ND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)

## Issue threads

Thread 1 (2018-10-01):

5V Power Supply Problems

chrissbarr, 2018-10-01:
Original note:

_Diodes are preventing board from being powered properly when USB power is not present. Removing diode D3 fixes it - best guess is reverse leakage through D3 prevents 5V regulator from operating, but need to investigate._

Okay. There seem to be a few conditions where the 5V buck regulator is behaving in a strange fashion - regulating to a much lower voltage (2-3V) instead of the 5V that it should be.

One of the conditions seems to be when the input voltage (Vin) exceeds some value. From some initial testing, the threshold voltage for this behaviour (Vth) seems to be inversely proportional to the current being drawn on the 5V rail. I.e.:

20mA draw, 5V regulator drops down to 2-3V when Vin > 24V
80mA draw, 5V regulator drops down to 2-3V when Vin > 17V

I should test with a wider range of load currents to see if that's a trend that continues.

Initial thinking was that the regulator was struggling with too light a load as Vin increased - but the above seems to have demonstrated that isn't so. I should test with a significantly larger load current (500mA+) just to make sure I haven't tested too limited a range - but regulators on previous boards work at these voltages / currents anyway.

The behaviour seems to relate to the feedback voltage divider, as there is some odd behaviour there. During normal operation, the regulator maintains a voltage of 0.8V across the divider - which with the specified resistor values regulates to ~ 5.2V. When Vin > Vth and the error state occurs, the divider voltage seems to be a different value - however, measuring that node with either a multimeter or an oscilloscope causes the regulator to start working again (or at least seems to significantly increase Vth - I seem to recall a test where the regulator remained in the error state with the multimeter connected if Vin was large enough, but I do not recall the measurement at the voltage divider in that test - that should be checked).

Why is the multimeter (presumably a > 1Mohm impedance to ground) making the regulator work correctly?

What is different in this regulator than on the previous RUMBA boards?

- Layout is updated (so maybe some coupling or noise somewhere the old design didn't have)
- PCB is 4 layer now (should be better but could be as above)
- A 4.7uF ceramic capacitor has been added to the regulator's output
   - Removing it does not change the behaviour
- Diode D2 prevents the stepper driver capacitors from feeding the 5V regulator (so capacitance on input is reduced from ~700uF to ~100uF)
   - Adding 470uF to main rail doesn't change behaviour

ongoing...

chrissbarr, 2018-10-03:
Cutting the trace to the feedback pin (which required desoldering and replacing the regulator IC) and replacing it with a wire link fixes the behaviour.

So either noise is coupling to the feedback trace, or the regulators are faulty. I'm assuming it's the trace, because:

- The trace runs directly underneath the regulator, and will be subjected to switching noise
- The signal is relatively high impedance
- The trace was routed differently in the previous design and this problem didn't occur there
- The fault occurs more often as the input voltage increases (so presumably switching noise increases)
- Connecting the signal to either GND or 5V by a large impedance (1Mohm resistor, multimeter, oscilloscope) causes the behaviour to return to normal for a while.

So the best course of action is probably just to redo that trace in the next revision, taking care to keep it away from noise sources, as in the previous design.

chrissbarr, 2018-10-08:
Feedback trace reworked in 1e07300974f51ee69adbfb81f0dc4cf37e811921.

Closed 2018-10-08.

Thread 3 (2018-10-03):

Inconsistent Stepper Driver Logic Voltage

chrissbarr, 2018-10-03:
Schematic describes stepper logic voltage defaults to 3.3V:

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

Actual PCB defaults to 5V:

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

Check which is correct and make consistent.

chrissbarr, 2018-10-08:
Fixed in 1e07300974f51ee69adbfb81f0dc4cf37e811921.

Closed 2018-10-08.

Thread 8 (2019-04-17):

PWM for Bltouch and LEDs on AUX pins?

wesk-ms, 2019-04-17:
Hello,

I built a Rumba32 board a couple months ago and it's been outstanding.  Very nice design...great work.

I'm trying to add a Bltouch and a string of neopixel LEDs to my corexy printer and not having any success.  I'm not seeing any PWM output on the pins PWM_1 or PWM_2.  I'm building a new build of Marlin every 3-4 days.  Also using the STM32Duino core and tools that I downloaded about a month ago.

The printer uses 6 steppers (tmc5160 stepsticks).  Bltouch device is genuine and v2.2.  It performs the power on self test correctly, but I'm not able to actuate the plunger via the LCD or with Gcode.

I'm really more concerned about getting the Bltouch working.  The pins I've tried for SERVO0_PIN are PD15, PD14. PD13, and PD12.  I've also tried simply specifying 62, 61, 60, and 59 in the pins_RUMBA32.h file, as well.

Something I found interesting...  I'm using VS Code to build Marlin, and Intellisense resolves PD15 to pin 63, and PD14 to 62, etc...  This is 1 pin off of the physical CPU connections.  I'm thinking that this has to be something funky with #includes since everything else on the board works flawlessly as is, despite Intellisense being 1 pin off for all 15 to 20 pins that I bothered to check.

I've looked through the timer definition code for this variant and I'm just not seeing any obvious errors.

--Any ideas what I might be overlooking?
--Have you or anyone else been successful in getting a Bltouch or LEDs to work on these pins?
--Is there a different pin I should be using for the BLtouch?

Thanks!
Wes

WK-MS, 2019-04-17:
@chrissbarr Do you have any thoughts as to why I'm unable to get a Bltouch working on the Rumba32 board on pins PD15, PD14, PD13, or PD12?

Thank you!

wesk-ms, 2019-04-28:
@chrissbarr , bumping this one again.  Would really like to get your insight on wether or not a timer change is needed to enable pwm output on PD15, PD14, PD13, and PD12.  I'll also go ahead and post this same question in the stm32duino repo.

Thanks!

chrissbarr, 2019-04-29:
Hi Wes,

Sorry that I haven't replied sooner. Too many notifications on GitHub - I missed your earlier messages. My apologies.

Very happy to hear that you've put together one of these boards and are enjoying it! That's great news. Glad that it is working well for you.

At the moment, I don't believe that PWM_1 or PWM_2 are configured to have PWM enabled in the stm32duino core. The relevant place where the PWM is configured is here:

https://github.com/stm32duino/Arduino_Core_STM32/blob/master/variants/RUMBA32_F446VE/PeripheralPins.c

PWM pins are defined from line 125 onwards:

```
const PinMap PinMap_PWM[] = {
  {PA_0,  TIM2,   STM_PIN_DATA_EXT(STM_MODE_AF_PP, GPIO_PULLUP, GPIO_AF1_TIM2, 1, 0)},  // TIM2_CH1
  //  {PA_0,  TIM5,   STM_PIN_DATA_EXT(STM_MODE_AF_PP, GPIO_PULLUP, GPIO_AF2_TIM5, 1, 0)},  // TIM5_CH1
  //  {PA_1,  TIM2,   STM_PIN_DATA_EXT(STM_MODE_AF_PP, GPIO_PULLUP, GPIO_AF1_TIM2, 2, 0)},  // TIM2_CH2
  {PA_1,  TIM5,   STM_PIN_DATA_EXT(STM_MODE_AF_PP, GPIO_PULLUP, GPIO_AF2_TIM5, 2, 0)},  // TIM5_CH2
  //  {PA_2,  TIM2,   STM_PIN_DATA_EXT(STM_MODE_AF_PP, GPIO_PULLUP, GPIO_AF1_TIM2, 3, 0)},  // TIM2_CH3 - STLink Tx
  //  {PA_2,  TIM5,   STM_PIN_DATA_EXT(STM_MODE_AF_PP, GPIO_PULLUP, GPIO_AF2_TIM5, 3, 0)},  // TIM5_CH3 - STLink Tx
  //  {PA_2,  TIM9,   STM_PIN_DATA_EXT(STM_MODE_AF_PP, GPIO_PULLUP, GPIO_AF3_TIM9, 1, 0)},  // TIM9_CH1 - STLink Tx
  //  {PA_3,  TIM2,   STM_PIN_DATA_EXT(STM_MODE_AF_PP, GPIO_PULLUP, GPIO_AF1_TIM2, 4, 0)},  // TIM2_CH4 - STLink Rx
  //  {PA_3,  TIM5,   STM_PIN_DATA_EXT(STM_MODE_AF_PP, GPIO_PULLUP, GPIO_AF2_TIM5, 4, 0)},  // TIM5_CH4 - STLink Rx
  //  {PA_3,  TIM9,   STM_PIN_DATA_EXT(STM_MODE_AF_PP, GPIO_PULLUP, GPIO_AF3_TIM9, 2, 0)},  // TIM9_CH2 - STLink Rx
  {PA_5,  TIM2,   STM_PIN_DATA_EXT(STM_MODE_AF_PP, GPIO_PULLUP, GPIO_AF1_TIM2, 1, 0)},  // TIM2_CH1
  //  {PA_5,  TIM8,   STM_PIN_DATA_EXT(STM_MODE_AF_PP, GPIO_PULLUP, GPIO_AF3_TIM8, 1, 1)},  // TIM8_CH1N
  {PA_6,  TIM13,  STM_PIN_DATA_EXT(STM_MODE_AF_PP, GPIO_PULLUP, GPIO_AF9_TIM13, 1, 0)},  // TIM13_CH1
  //  {PA_6,  TIM3,   STM_PIN_DATA_EXT(STM_MODE_AF_PP, GPIO_PULLUP, GPIO_AF2_TIM3, 1, 0)},  // TIM3_CH1
  {PA_7,  TIM14,  STM_PIN_DATA_EXT(STM_MODE_AF_PP, GPIO_PULLUP, GPIO_AF9_TIM14, 1, 0)},  // TIM14_CH1
  //  {PA_7,  TIM1,   STM_PIN_DATA_EXT(STM_MODE_AF_PP, GPIO_PULLUP, GPIO_AF1_TIM1, 1, 1)},  // TIM1_CH1N
  //  {PA_7,  TIM3,   STM_PIN_DATA_EXT(STM_MODE_AF_PP, GPIO_PULLUP, GPIO_AF2_TIM3, 2, 0)},  // TIM3_CH2
  //  {PA_7,  TIM8,   STM_PIN_DATA_EXT(STM_MODE_AF_PP, GPIO_PULLUP, GPIO_AF3_TIM8, 1, 1)},  // TIM8_CH1N
  {PA_8,  TIM1,   STM_PIN_DATA_EXT(STM_MODE_AF_PP, GPIO_PULLUP, GPIO_AF1_TIM1, 1, 0)},  // TIM1_CH1
  {PA_9,  TIM1,   STM_PIN_DATA_EXT(STM_MODE_AF_PP, GPIO_PULLUP, GPIO_AF1_TIM1, 2, 0)},  // TIM1_CH2
  {PA_10, TIM1,   STM_PIN_DATA_EXT(STM_MODE_AF_PP, GPIO_PULLUP, GPIO_AF1_TIM1, 3, 0)},  // TIM1_CH3
  {PA_11, TIM1,   STM_PIN_DATA_EXT(STM_MODE_AF_PP, GPIO_PULLUP, GPIO_AF1_TIM1, 4, 0)},  // TIM1_CH4
  {PA_15, TIM2,   STM_PIN_DATA_EXT(STM_MODE_AF_PP, GPIO_PULLUP, GPIO_AF1_TIM2, 1, 0)},  // TIM2_CH1
  //  {PB_0,  TIM1,   STM_PIN_DATA_EXT(STM_MODE_AF_PP, GPIO_PULLUP, GPIO_AF1_TIM1, 2, 1)},  // TIM1_CH2N
  //  {PB_0,  TIM3,   STM_PIN_DATA_EXT(STM_MODE_AF_PP, GPIO_PULLUP, GPIO_AF2_TIM3, 3, 0)},  // TIM3_CH3
  {PB_0,  TIM8,   STM_PIN_DATA_EXT(STM_MODE_AF_PP, GPIO_PULLUP, GPIO_AF3_TIM8, 2, 1)},  // TIM8_CH2N
  //  {PB_1,  TIM1,   STM_PIN_DATA_EXT(STM_MODE_AF_PP, GPIO_PULLUP, GPIO_AF1_TIM1, 3, 1)},  // TIM1_CH3N
  //  {PB_1,  TIM3,   STM_PIN_DATA_EXT(STM_MODE_AF_PP, GPIO_PULLUP, GPIO_AF2_TIM3, 4, 0)},  // TIM3_CH4
  {PB_1,  TIM8,   STM_PIN_DATA_EXT(STM_MODE_AF_PP, GPIO_PULLUP, GPIO_AF3_TIM8, 3, 1)},  // TIM8_CH3N
  {PB_2,  TIM2,   STM_PIN_DATA_EXT(STM_MODE_AF_PP, GPIO_PULLUP, GPIO_AF1_TIM2, 4, 0)},  // TIM2_CH4
  {PB_3,  TIM2,   STM_PIN_DATA_EXT(STM_MODE_AF_PP, GPIO_PULLUP, GPIO_AF1_TIM2, 2, 0)},  // TIM2_CH2
  {PB_4,  TIM3,   STM_PIN_DATA_EXT(STM_MODE_AF_PP, GPIO_PULLUP, GPIO_AF2_TIM3, 1, 0)},  // TIM3_CH1
  {PB_5,  TIM3,   STM_PIN_DATA_EXT(STM_MODE_AF_PP, GPIO_PULLUP, GPIO_AF2_TIM3, 2, 0)},  // TIM3_CH2
  {PB_6,  TIM4,   STM_PIN_DATA_EXT(STM_MODE_AF_PP, GPIO_PULLUP, GPIO_AF2_TIM4, 1, 0)},  // TIM4_CH1
  {PB_7,  TIM4,   STM_PIN_DATA_EXT(STM_MODE_AF_PP, GPIO_PULLUP, GPIO_AF2_TIM4, 2, 0)},  // TIM4_CH2
  //  {PB_8,  TIM10,  STM_PIN_DATA_EXT(STM_MODE_AF_PP, GPIO_PULLUP, GPIO_AF3_TIM10, 1, 0)},  // TIM10_CH1
  //  {PB_8,  TIM2,   STM_PIN_DATA_EXT(STM_MODE_AF_PP, GPIO_PULLUP, GPIO_AF1_TIM2, 1, 0)},  // TIM2_CH1
  {PB_8,  TIM4,   STM_PIN_DATA_EXT(STM_MODE_AF_PP, GPIO_PULLUP, GPIO_AF2_TIM4, 3, 0)},  // TIM4_CH3
  {PB_9,  TIM11,  STM_PIN_DATA_EXT(STM_MODE_AF_PP, GPIO_PULLUP, GPIO_AF3_TIM11, 1, 0)},  // TIM11_CH1
  //  {PB_9,  TIM2,   STM_PIN_DATA_EXT(STM_MODE_AF_PP, GPIO_PULLUP, GPIO_AF1_TIM2, 2, 0)},  // TIM2_CH2
  //  {PB_9,  TIM4,   STM_PIN_DATA_EXT(STM_MODE_AF_PP, GPIO_PULLUP, GPIO_AF2_TIM4, 4, 0)},  // TIM4_CH4
  {PB_10, TIM2,   STM_PIN_DATA_EXT(STM_MODE_AF_PP, GPIO_PULLUP, GPIO_AF1_TIM2, 3, 0)},  // TIM2_CH3
  {PB_13, TIM1,   STM_PIN_DATA_EXT(STM_MODE_AF_PP, GPIO_PULLUP, GPIO_AF1_TIM1, 1, 1)},  // TIM1_CH1N
  {PB_14, TIM12,  STM_PIN_DATA_EXT(STM_MODE_AF_PP, GPIO_PULLUP, GPIO_AF9_TIM12, 1, 0)},  // TIM12_CH1
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
wesk-ms, 2019-04-29:
Thanks for the reply.  No need to apologize, I assumed you were busy.

Thanks for confirming that not having these pins set up for PWM in PeripheralPins.c is the cause of the behavior I'm seeing.  I tried enabling them, to no avail, but I think I may have caused a timer conflict in doing so.  I noticed that in order to get add the pins I wanted, I was likely going to have to redefine a chain of other pins to ensure no sharing of timers.

I agree that the bltouch seems to be finicky and that getting Marlin to simply output a PWM signal when issuing a bltouch command is my next step.  Fortunately, I'm not using the serial pins on exp3, so that's where I'll go next.  Once I get that working, I'll figure out how to correctly set up the other pins in PeripheralPins.c.

Lastly, can you tell me where you're actually mapping the pin names (like PD_0, PC_5, etc...) to the physical pin numbers on the processor?  I thought that would be done in variant.h, but it's not.  I recall some code elsewhere that looked like it was doing the conversion, but I'm not sure.  Specifically, where does PD_15 get mapped to physical pin 62?

Thanks again for your help!  I was going nuts trying to get my DUE+RADDS board to perform well and work reliably, so I finally decided to scrap that and find a better 32bit board.  You designed the perfect solution IMO, and I think it should become the new 'standard' for 3D printer controllers.

chrissbarr, 2019-04-29:
No worries, happy to help.

The pin mapping is done in the variant.cpp file, starting from about line 25, here:

https://github.com/stm32duino/Arduino_Core_STM32/blob/master/variants/RUMBA32_F446VE/variant.cpp

It's not immediately obvious that that's what you're after, because the way the pins are defined in stm32duino you don't actually see the pin numbers. The pin numbers are implicit in the list - so the first pin is D0, the second is D1, and so on.

The numbering is somewhat arbitrary, and there's _no correlation_ between the numbers assigned to the pins and their actual physical numbering - I simply chose to go from PA_0 in order. This may be something that's tripped you up - to my knowledge, the physical pin numbers are not used anywhere in the stm32duino core (or at least, not for this board). You can use either the port/pin definitions (i.e. PA0, PD15, etc), or the number mapped in the above file - which for PD15 is 63.

It would be nice to have the stm32duino pin numbers correspond to the physical package numbers, but I'm not sure if this is doable - specifically, I'm not sure if it's possible to have gaps in the pin numbers, as would be needed to allow for power and other non-gpio pins.

Hope that helps! Let me know if you need any more info.

DropbearNinja, 2019-11-27:
Hi @WK-MS did you get bltouch working on the rumba32? I'm having same issue

WK-MS, 2019-11-27:
No, I didn’t.  I think the issue was in the STM32 core.  PWM timer related.  The Rumba32 board is incredible, but because of that issue I moved to a different board and had no problems.  I’ve also moved away from Marlin and I’m using Klipper with much better results.  You might want to try MK4Duo firmware.  The owner of that code has recently ported it to STM32…specifically for the Rumba32 board.

Thanks,
Wes

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

DropbearNinja, 2019-12-05:
Hi @chrissbarr - could you please have a look at this? I've spent about 2 weeks trying literally everything.... I looked at the data sheet, pin PD15 is alt fn of TIM4, I created that in peripheralpins
{PD_15,  TIM4,   STM_PIN_DATA_EXT(STM_MODE_AF_PP, GPIO_PULLUP, GPIO_AF2_TIM4, 1, 0)},
And tried, well basically everything, even stuff that didn't make sense.
The rumba32 is a great board, but extra PWM functionality is a necessity, and at the moment non functioning....

DropbearNinja, 2019-12-05:
... 2 weeks, I post, and then 1 hour later, get it working...

DropbearNinja, 2019-12-05:
In
> C:\Users\xxx\AppData\Local\Arduino15\packages\STM32\hardware\stm32\1.7.0\variants\RUMBA32_F446VE

change
`#define TIMER_SERVO             TIM7`
to
`#define TIMER_SERVO             TIM4`
(reason: PD15 which is PWM2 is connected to TIM4 as per stm32f446 datasheet)

In:

> C:\Users\xxxxx\AppData\Local\Arduino15\packages\STM32\hardware\stm32\1.7.0\variants\RUMBA32_F446VE\PeripheralPins.c

change:
`//  {PB_9,  TIM4,   STM_PIN_DATA_EXT(STM_MODE_AF_PP, GPIO_PULLUP, GPIO_AF2_TIM4, 4, 0)},  // TIM4_CH4`
to:
`{PD_15,  TIM4,   STM_PIN_DATA_EXT(STM_MODE_AF_PP, GPIO_PULLUP, GPIO_AF2_TIM4, 4, 0)},  // TIM4_CH4`

In Marlin in:
`..\Marlin-2.0.x\Marlin\src\pins\stm32\pins_RUMBA32.h`
add
`#define SERVO0_PIN	PD15`

That's it... that's all you need to do, and PWM works on PD15, and hence bltouch works fine

Closed 2020-07-08.

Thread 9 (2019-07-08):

Error in BoM

leseaw, 2019-07-08:
Hello,

Point 6 in RUMBA32_v1_0E_BOM.xlsx
Name:
CAP CER 4.7UF 10V X7R 0603
PartNumer:
	TDK
C1608X7R1C105K080AC
C Series 0603 1 uF 16 V ±10 % Tolerance X7R SMT Multilayer Ceramic Capacitor

i think Name is wrong or partnumer?

chrissbarr, 2019-07-08:
Hi @leseaw,

Yes, you're right, there's an issue with this line in the BOM. We noticed this recently but it hasn't been corrected yet. I don't believe we were able to find a part matching the specifications we gave in an 0603 package - in our current batch of boards we have used the following part:

C1608X7S1A475K080AC - CAP CER 4.7UF 10V X7S 0603 (Digikey [445-14258-1-ND](https://www.digikey.com/product-detail/en/tdk-corporation/C1608X7S1A475K080AC/445-14258-1-ND/3955924))

That matches the capacitance, voltage, and package, but is dropping from an X7R to X7S. This is just a small tolerance change and won't be a problem in this application, as the capacitance value is not critical.

We will likely be updating the BOM to this or a similar part soon.

leseaw, 2019-07-08:
Hi @chrissbarr ,

Are there any more changes which are still wrong in the BoM?

chrissbarr, 2019-07-08:
Not that I am aware of. Apart from that one exception, we are using the BOM as included without any changes.

leseaw, 2019-07-08:
okay thanks @chrissbarr
And read your E-Mails :)

chrissbarr, 2019-07-08:
No worries @leseaw - just to be sure, you did get my reply last week?

leseaw, 2019-07-08:
@chrissbarr yes :) this i s why i write here. i answer you.

leseaw, 2019-07-09:
@chrissbarr my mails to you come back :( time out from your mailserver.

Closed 2019-07-08.

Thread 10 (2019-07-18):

BoM and Parts D3 D4 D5 D15 component is SS24FL diode

leseaw, 2019-07-18:
Hi Chris,

i think thats wrong or?

D3, D4, D5, D15, the BOM component size is 5.4 * 1.8mm, while Gerber pad size is 3.7 * 1.2mm, not match.

chrissbarr, 2019-07-18:
Hi @leseaw,

From what I can see in the SS24FL [datasheet](https://www.onsemi.com/pub/Collateral/SS26FL-D.PDF), it measures a maximum of 3.90 x 1.95mm. Maybe double-check where the 5.40 x 1.80mm size you've mentioned comes from, as I couldn't find it.

The pads we have are a little smaller than the recommended footprint and don't extend beyond the diode's leads, but we haven't had any trouble with soldering these parts (reflow has always worked fine and I've assembled/reworked a number of boards by hand without noticing a problem here). We've used this same footprint & part since V1.1 of the RUMBA+ boards, and I don't believe we've ever seen a problem with these diodes - so I don't think you will run into any trouble there.

I'll take a look at the pads during the next revision, but I'm hesitant to do a revision just for this as it's always worked without issue.

Hope that helps!

leseaw, 2019-07-19:
My mistake, ashes on my head :(

Closed 2019-07-19.

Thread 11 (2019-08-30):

platformIO setup for Marlin

wap32, 2019-08-30:
Hello,

I just got myself a RUMBA32 board and am currently setting it up with Marlin.
The WiKi is helpful enough to guide through the Arduino IDE setup, and this works fine and I'm able to compile and upload without issues (so far).

However, I would like to get Marlin working with platformIO, and here I've been facing some issues.

Is there a known good platformio.ini env setup for Marlin that compiles properly with RUMBA32?

I think this would be a good addition to the WiKi documentation, as platformIO tends to be more straightforward to use once set up properly, and more portable as it does not depend on an existing properly configured Arduino IDE.

lei111, 2019-11-23:
I also encountered the same problem and hope to provide a configuration example. Thank you

wap32, 2019-12-10:
I forgot to update this issue, I ended up finding a working config for platformio, at least as of a couple of months ago (have not tested with latest Marlin build).

```
#
# RUMBA32
#
[env:rumba32_f446ve]
platform      = ststm32
framework     = arduino
board         = rumba32_f446ve
build_flags   = ${common.build_flags}
  -DSTM32F4xx
  -DARDUINO_RUMBA32_F446VE
  -DARDUINO_ARCH_STM32
  "-DBOARD_NAME=\"RUMBA32_F446VE\""
  -DSTM32F446xx
  -DUSBCON
  -DUSBD_VID=0x0483
  "-DUSB_MANUFACTURER=\"Unknown\""
  "-DUSB_PRODUCT=\"RUMBA32_F446VE\""
  -DHAL_PCD_MODULE_ENABLED
  -DUSBD_USE_CDC
  -DDISABLE_GENERIC_SERIALUSB
  -DHAL_UART_MODULE_ENABLED
  -Os
lib_deps      = ${common.lib_deps}
lib_ignore    = Adafruit NeoPixel
src_filter    = ${common.default_src_filter} +<src/HAL/HAL_STM32> +<src/HAL/HAL_STM32_F4_F7> -<src/HAL/HAL_STM32_F4_F7/STM32F7>
monitor_speed = 500000
upload_protocol = dfu
```

deruben900, 2020-01-21:
Have you been able to use the board with the latest Marlin version (2,0) with platformio?
I am able to build, but not upload it firmware to my board.

capibara1, 2020-06-01:
I have not been able to compile Marlin 2.0.x (2.0.5.3 as of today) or bugfix-2.0.x at all. Whether is it with the Arduino IDE or via Platform IO. The platform.ini entry for the RUMBA32 that @wap32 provided seems to be the one to use (better than the default entry that comes with Marlin) but still doesn't produce a successful compile.

chrissbarr, 2020-06-02:
The PlatformIO config included with the current `bugfix-2.0.x` Marlin branch is working for me - I've put together some instructions here: https://github.com/Aus3D/RUMBA32/issues/22#issuecomment-637216106

chrissbarr, 2020-07-07:
I've updated the [https://github.com/Aus3D/RUMBA32/wiki](wiki) with instructions for using PlatformIO.

Closed 2020-07-07.

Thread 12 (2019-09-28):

EEPROM I2C

MagoKimbra, 2019-09-28:
In the scheme there seems to be the I2C eeprom, but I can't find it, I did the scanning on the port, but nothing.
There is and if there is that address has, normally it should be 0x50.
Thanks! |

chrissbarr, 2019-09-28:
Hi @MagoKimbra,

There's a footprint on the PCB to suit an I2C EEPROM, but no actual EEPROM IC has been installed on the boards we are shipping. It is not included because the flash emulation in the Marlin STM32 HAL seemed to make it unnecessary. Could the flash emulation work for what you need?

We are still very early in the life of these boards - if you have feedback that you think the EEPROM IC would be a good thing to have, let me know, and we will take that into account in future revisions.

Let me know if you'd like any more information!

MagoKimbra, 2019-09-28:
Hi, I don't use Marlin, I use MK4duo, a firmware born by Marlin 5 years ago, but completely different today.
I'm starting to program on Rumba32 and I'm on the right track almost everything works today, except for communicating to the SPI TMC2130 drivers and the EEPROM.
For the driver I tried to install Marlin 2.0 to check and even that doesn't communicate, so I think it's the driver I use for tests, I bought another one, see.
For the EEPROM thinking that there was already, I was going crazy looking for the address, but if it's not there it's normal.
EPPROM flash, yes good, now I have to try to see if I can make it go like on Arduino DUE, but at least on this one if you download a new firmware even if the EEPROM configuration has not changed you lose it anyway. I prefer the I2c at least it is always present after a new download ...
Hello and thanks.

chrissbarr, 2019-09-28:
Hi @MagoKimbra,

Ah, I understand about MK4duo (I thought your username was familiar, should have realised!).

We have had someone else report having trouble with TMC2130 SPI in the last few days, I am looking into it at the moment to see what the problem might be - so, it might not just be you. I will let you know if there is any discovery.

Sorry for the confusion about the EEPROM. You make a good point about losing the configuration, I will make a note and we will look at adding the IC back for future batches.

For adding one yourself, there are pads for a SOT-23-5 EEPROM and an 0603 capacitor (100nF or similar), here:

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

The pinout is like this:

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

The pinout was to suit the 24LC16BT-I/OT I2C EEPROM, but it is a common footprint I believe so other parts may work as well. The ceramic capacitor is recommended, anything in an 0603 size, 100nF - 1uF, 6.3V or greater should work fine (probably can work without it - but for production, we would definitely include it).

Let me know if you would like any more information.

MagoKimbra, 2019-09-28:
I'm glad you know me.
Unfortunately today Marlin passed me for processors, I was the first with a firmware based on marlin to use Arduino DUE, but then I stopped, not having much time and above all because I'm alone. Today Marlin has many supported processors, so I decided to shoot with STM32 and the rumba32 which I think is an excellent card.
I hope the SPI driver problem can be solved easily.
Meanwhile, I can hardly do with the flash ram for EEPROM emulation and then we see the next developments you will make ..
Thank you and good day.

MagoKimbra, 2019-09-28:
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

I know that the problem is this the 4 pins SDI, SCK, CS, and SDO are sequential and are the driver 2 pin 4 4 5, while from the diagram, SDO you put it on SLEEP pin 6, at least I see it from scheme.
I hope I'm wrong, but if it were so it's a mess to edit on the card ...

chrissbarr, 2019-09-28:
Hi @MagoKimbra,

You're right - I've just found the same thing here, and have confirmed it in testing.

Marlin will write to the drivers OK, but can not receive anything from them. We used the SPI drivers in testing, but looking at our test procedure we only tested writing to them / adjusting settings, nothing that required the feedback.

I'm don't think there's an easy fix on the current boards, as the tracks are under the jumper pins and can't easily be cut / modified. Some way of jumping the outermost pins should work, but is not easy to do.

I'll keep looking into this and will see if there are any other solutions... We can get this fixed in the next batch of boards, but will have to find another solution for anyone else with a current board.

Thanks for investigating!

chrissbarr, 2019-09-28:
I've added a notice to our product page for RUMBA32. Tomorrow I will look more closely and see if there is a fix to get both SPI and normal modes working.

Sorry for the trouble you've run into here! We will get this fixed in the next batch, and if you want we can exchange your board for an updated one then.

chrissbarr, 2019-10-14:
Just in case anyone else runs across this issue here, our current documentation for the SPI fix is below:

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

MagoKimbra, 2019-10-14:
Ok, perfect ... Yesterday I run my delta with the rumba32 and everything goes perfectly, bltouch, sd, TMC2130, DHT, Nextion, etc etc.
Thanks, and I ask you for a courtesy, could you mention the MK4duo firmware that runs on your card?
I thank you if you do.
https://github.com/MKFirmware/MK4duo

chrissbarr, 2019-10-14:
Hi @MagoKimbra,

Yes, I enjoyed that video you linked me to - it looks like everything is running very well with the MK4duo firmware. Congratulations on getting it all working well! I'd be happy to mention the MK4duo firmware, I'll add a list of supporting firmwares to the main Git readme shortly.

leseaw, 2019-11-02:
its the same :(

robustini, 2019-12-19:
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

CGuasco, 2020-01-09:
Hello, the eeprom you recommend (24lc16) has a software protocol different from the i2c standard: the first byte must be 0101 plus the page (3 bits), while the standard protocol is 0101 plus 3 bits of the hardware address. since is on the same i2c bus, it would not be possible to insert other peripherals.
Putting a 24lc256 works perfectly, but it has a totally different footprint (8 pins instead of 5).
Am I wrong?
I only see one i2c bus.

chrissbarr, 2020-01-10:
Hi @CGuasco,

My reading of the 24LC16 datasheet is that it will consume addresses 0x50 - 0x57 on the I2C bus. This means it would not be possible to use the 24LC16 and another device with an address in that range on the same bus. Devices with addresses outside of that range should not have a conflict.

You are correct that there is only one I2C bus broken out on the RUMBA32 board.

I believe there are a number of I2C EEPROM ICs that adhere to both the addressing protocol you desire and the SOT-23-5 footprint on RUMBA32. I believe the [24AA32AT](https://www.digikey.com.au/product-detail/en/microchip-technology/24AA32AT-I-OT/24AA32AT-I-OTCT-ND/2059999) is one such part, I'd suggest checking if that looks suitable to you.

phongshader, 2020-05-09:
If I were to solder on an eeprom chip and capacitor, as you intended, which chip would you recommend? ‎24AA32AT or 24LC16BT?

chrissbarr, 2020-05-09:
Hi @phongshader,

Any of the above should be suitable, however I have not tested the 24AA32AT so would recommend that last.

I am planning to include the [24LC64T-I/OT](https://www.digikey.com/product-detail/en/microchip-technology/24LC64T-I-OT/24LC64T-I-OTCT-ND/2039861) (bigger, 8kB cousin of the 24LC16BT) on future versions of RUMBA32. I have tested this part and it works with Marlin's I2C EEPROM implementation with no modifications required. Can confirm pinout etc. match the RUMBA32 boards in circulation (this is what I am testing on). This would be my first recommendation if available.

phongshader, 2020-06-04:
Hi  @chrissbarr
I received my board yesterday and installed the eeprom chip. I have a question about the orientation of the eeprom chip on the board. I paid no attention to any markings on the board since the pins are asymmetrical and can only be installed one way. After the chip was installed I took a closer look at the markings on the board and the chip. If I were to install the chip based on the board and chip markings I would have to install the chip upside down.
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 I know this is a MKS board but I just wanted to get your feedback.

chrissbarr, 2020-06-04:
Hi @phongshader,

Hmm, I've had a look at the datasheets for the 24AA32AT and [24LC64T-I/OT](http://ww1.microchip.com/downloads/en/DeviceDoc/21189T.pdf), and the datasheets actually don't show the SOT-23 packages as having any polarity marking. All other packages do - see below:

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

This is probably because the SOT-23 is smaller than the other packages, and are polarised anyway, so this has not been included. I would guess that the mark on the actual package could just be from the moulding process (I forget the term - but many components have 2 marks, one from manufacture, and another printed on for polarity. Check the STM32 on the board, I believe it has two marks that are in different corners.)

I agree that the pinout should be correct the way you have installed it. If you run into trouble, let me know and we'll figure it out.

phongshader, 2020-06-04:
I made my conclusion based on the silk screen image
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
found here http://ww1.microchip.com/downloads/en/DeviceDoc/05L_SOT-23_OT_C04-00091f.pdf
Seems like they would know although nothing is explicitly stated.

Thanks for checking in.

chrissbarr, 2020-06-05:
Looks good from that image then. As mentioned previously, I'm using the 24LC64T-I/OT myself on one of these boards for testing purposes and it's been happy in this orientation.

All of the I2C EEPROM ICs I can find from Microchip in SOT-23 look to have the same pinout, so I'd say it's something of a defacto standard at least for this manufacturer (I haven't looked around much beyond that).

phongshader, 2020-06-09:
how do I enable eeprom in firmware?
`#define EEPROM_SETTINGS     // Persistent storage with M500 and M501
//#define DISABLE_M503        // Saves ~2700 bytes of PROGMEM. Disable for release!
#define EEPROM_CHITCHAT       // Give feedback on EEPROM commands. Disable to save PROGMEM.
#define EEPROM_BOOT_SILENT    // Keep M503 quiet and only give errors during first load
#if ENABLED(EEPROM_SETTINGS)
  #define EEPROM_AUTO_INIT  // Init EEPROM automatically on any errors.
#endif`
when issuing M500
`>>> m500
SENDING:M500
echo:No EEPROM.`
The components I used are CAP CER 1UF 6.3V X7R 0603 and 24LC64T-I/OT

chrissbarr, 2020-06-10:
Try this:
```
#define I2C_EEPROM
#define MARLIN_EEPROM_SIZE 0x2000             // 8KB (24LC64T-I/OT)

#define EEPROM_SETTINGS     // Persistent storage with M500 and M501
//#define DISABLE_M503        // Saves ~2700 bytes of PROGMEM. Disable for release!
#define EEPROM_CHITCHAT       // Give feedback on EEPROM commands. Disable to save PROGMEM.
#define EEPROM_BOOT_SILENT    // Keep M503 quiet and only give errors during first load
#if ENABLED(EEPROM_SETTINGS)
  //#define EEPROM_AUTO_INIT  // Init EEPROM automatically on any errors.
#endif
```

Closed 2020-07-08.

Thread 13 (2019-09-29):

TMC220x on-board UART compability

Blaster1920, 2019-09-29:
Hi,
by having a look at the design I noticed that it is missing an important feature to correctly drive the TMC2208 and TMC2209 drivers directly from the MCU. In fact, it looks like you omitted the possibility of choosing between SPI and UART mode: is there a particular reason why you preferred going this way?
Thank you in advance for your time.

chrissbarr, 2019-09-30:
Hi @Blaster1920,

Short answer: supporting the UART drivers didn't seem feasible within the constraints of this board, but if you can see a way to make it work let me know and we'll take it into consideration.

My understanding is that the UART-based TMC drivers require two communication pins (TX and RX) per driver. Please correct me if this is incorrect. The SPI-based TMC drivers require three pins shared among all drivers (MISO, MOSI, SCK) and 1 pin for each driver (CS). On the current design, there are not enough spare GPIO to support adding an extra pin to each driver (also it would be tough to route an extra signal to each driver socket).

If there's a way that the UART drivers can work with just a simple jumper using the signals that are already routed to each socket, then it's definitely something I'd be interested in exploring. At the moment, each stepper driver has the following pins/signals:
- STEP
- DIRECTION
- ENABLE
- CHIP SELECT
- MISO (shared)
- MOSI (shared)
- SCK (shared)

So, we don't have two pins per driver (outside the usual STEP/DIR/EN) to act as RX & TX. Is it possible to control the TMC2208 with only TX (i.e. no feedback)? If so, it might be possible to use the CHIP SELECT signal as a soft UART TX for that purpose. I'm not familiar enough with the state of TMC220X firmware support to say.

Let me know what you think, if you have a way of making it work I'd love to get it included in the design.

Blaster1920, 2019-09-30:
Hi @chrissbarr,
thank you for the prompt and detailed response.
I've been looking for possible solutions, but so far nothing seems to be what we need, even though there may be a couple of possibilities:

- [https://github.com/MarlinFirmware/Marlin/issues/14208](url) a bug report that may be fixed by now for using Tx only mode.

- In the STM32F446VE datasheet 6 USARTs are being mentioned, which ones would you have free if you add an onboard microsd reader? Would it be possible to share the same pins for both usb and microsd reader by enabling usb only when the microsd is not inserted?

- [https://www.instructables.com/id/UART-This-Serial-Control-of-Stepper-Motors-With-th/](url) an extra link that may be handy.

- Last but not the least: what if you enable the UART to TMC22xx on-board only for 4 drivers? That's usually the typical need when tmc2208 are used. (x y z e0)

Let me know.

sverd, 2020-08-03:
Hi,
I noticed that in newer revisions the on-board UART seems to have been fixed/added. I could however not completely figure out how this was done. The thing is that I have a 1.0 version of the board and I'm wondering whether it is possible to "fix" that board to get UART working with the stepper drivers. Is it possible to get UART working with possibly a few  small modifications? (mainly asking because I saw the fix to get SPI communication with the stepper drivers working which is very doable)

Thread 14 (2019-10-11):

Exp3 pinout

MagoKimbra, 2019-10-11:
Hi, I'm here again to ask you something, I think it's another mistake I think of drawing.
The pins in exp3 5 and 6 PWM 1 and PWM2 are on processor PD14 and PD15, so pins 13 and 14 what are they? PD12 and PD13? On the drawing they are called PD14 PD15 ...
If they are PD12 and PD13, you know if they can be used as interrupts, STM32 can use all pins as interrupts, if you know it, otherwise I try ...

chrissbarr, 2019-10-13:
Hi @MagoKimbra,

You're right again! Yes, PD14 and PD15 are misnamed, they should be PD12 and PD13.

I've updated the schematic and images to show this correctly now.

All pins can be used as interrupts, but I believe only one of each pin number (i.e. can't use both PA**0** and PB**0** as interrupt - only PA0 or PB0 or PC0 etc...). So there are 16 pin-change interrupts available (Px0 to Px15). I included a table in the schematic showing one way the pins can be used without conflicting:

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

So, if you want to use interrupts for X-MIN and X-MAX (PB12 and PB13) then there are no interrupts available for PD12 and PD13. To use interrupts on PD12 and PD13, there can be no interrupts on any other Px12 and Px13 pins.

MagoKimbra, 2019-10-13:
Hi, please check carefully, because yesterday I tried pin by pin and the correspondence is not that.
What I found was this:
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

chrissbarr, 2019-10-13:
Hi @MagoKimbra,

It's easy to get mixed up here, so I'll put together all the info I have and we'll see if we can get this figured out.

Here's an image showing the pins in the schematic and on the PCB:

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

Also included is the pin definition in the Arduino_Core_STM32 variant.h file, which sets the Arduino pin numbers for the STM32 pins.

The numbers in your image - are they the Arduino pin numbers? The Arduino pin numbers should be:

PD12 (previously PD14 as in your image) - 60
PD13 (previously PD15 as in your image) - 61
PWM_1 (PD14) - 62
PWM_2 (PD15) - 63

The first three are the same as in your image, but PWM_2 is different. Are you sure that PWM_2 corresponds to 59? I can't find this in my checking, but I am prepared to be wrong.

MagoKimbra, 2019-10-13:
Yes, I was wrong on 59, I tried only 60, 61 and 62 so I had one pin left and I wrote 59, in fact it's 63, perfect now everything exp3 matches me.

MagoKimbra, 2019-10-13:
https://www.facebook.com/MK4duo/videos/857002628047547/
But you must write to group for see the video...

chrissbarr, 2020-07-07:
I'm going to close this issue out now, but for future reference the pinout of the EXP3 header is:

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

I've added a pinout image to the main readme.

Closed 2020-07-07.

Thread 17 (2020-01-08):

Stepper sockets in Rev E still defect

repetier, 2020-01-08:
Hi @chrissbarr ,
I purchased a RUMBA32 Rev E to add support for your board to Repetier-Firmware V2 (https://github.com/repetier/Repetier-Firmware/tree/dev2) and it is working already very good.

I read that up to Rev D there is a problem with SPI MOSI pin connected to wrong pin header, so was lucky to have a "fixed" board. But after searching for hours I detected that reading the driver does not work due to same pin switch. So not sure if it was meant to be fixed or if that was Rev E in old version or if it is different producer since I ordered it in Germany, but it contains your domain on backside.

Beside that it would be nice if you would add a reference to the additional firmware possible with that board.

leseaw, 2020-01-08:
Rev E has this error too :(

chrissbarr, 2020-06-02:
Hi @repetier, @leseaw.

Sorry there was no reply on this earlier. I have not been getting notifications from this repo, and am going through at the moment trying to get caught up.

To confirm, the SPI defect is present in v1.0E. I have put together a central FAQ issue on this here, for future reference: https://github.com/Aus3D/RUMBA32/issues/23

Really cool to hear that the board is being supported within Repetier-Firmware V2! I will give it a go when I receive the next batch of boards.

chrissbarr, 2020-06-02:
I have added a link to Repetier-Firmware in the readme:

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

Let me know if you would prefer different wording or a different URL linked to.

Closed 2020-06-02.

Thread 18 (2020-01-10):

MKS TFT32_L V4.0 compatibility

rubenoosterwijk, 2020-01-10:
Is the Rumba32 board not compatible with the Makerbase Touchscreens LCDs?
The Rumba+ board did have a AUX1 port.
How can i fix this?

kai658, 2020-02-26:
MKS RUMBA32, which I bought at maker base, is supported

chrissbarr, 2020-07-08:
Hi @rubenoosterwijk,

I'm hoping you've solved this by now, but will post an answer in case anyone comes across this for future reference.

The RUMBA32 board has the same expansion headers that RUMBA+ had -  EXP1, EXP2 and EXP3.

I'm not familiar with an AUX1 port on RUMBA+ - perhaps this is something that another manufacturer added to their version?

From what I can see, the MKS TFT displays need 5V, GND, UART TX and UART RX. You can access all of these on EXP3 - refer to the image below:

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

I'm not sure what type of cable the display comes with. You'd need to find a way to connect the correct pins.

Closed 2020-07-08.

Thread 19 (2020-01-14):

USB Power

CGuasco, 2020-01-14:
I would like to prevent the card from being powered by USB.
My printer is always connected to a Raspberry with the Repetier Server always on (connected to multiple printers).
This way the board can never be OFF; more. most important, USB is not enough to power the board with Nextion and continue to go in protect mode and return to 5V, so pwr is flashing.
Usually I use a USB Cable without 5 V, but in this case USB/Serial chip is not powered.
Is it sufficient to eliminate the fuse F3 (I suppose it is the one close to pin 1 of the USB header) there are drawbacks if there is USB connected (USB / Serial U5 chip powered) and card off?
Alternatively bypass D4 or revert it (USB chip powered by the board) and use a special USB cable (without 5V)
(The first option is preferrable)
Tks, Carlo
Tks

chrissbarr, 2020-06-02:
Hi @CGuasco, sorry for the very late reply.

Any of the methods you propose should work. However, using the cable without 5V will weaken the ESD protection on the board, so I would suggest either removing F3 or D4.

Closed 2020-06-02.

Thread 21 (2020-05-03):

Connection fails with Octoprint

McPrince96, 2020-05-03:
HI,

i've set up my new Rumba32 board and installed it in my printer. I've got Octoprint and Octoscreen installed on a raspberry pi which links to the board througn a usb cable.

My previous board was a rumba+ and connected just fine but this board won't connect to Octoprint. I tried it in the default mode and DFU mode but neither one of them work.

capibara1, 2020-05-31:
You will not get any support from Aus3D. I was able to compile Marlin-bugfix-2.0.0 in Nov 2019 just fine. Now can't even compile at all following the exact instructions on the website.
No response from Aus3D for months.

chrissbarr, 2020-06-01:
Hi @McPrince96,

Are you able to talk to the RUMBA32 board from a computer over the USB connection (i.e. using any printer host software - Pronterface, Simplify3D, etc?).

I would suggest you need to work out if the firmware on the board is running correctly and communicating over USB - so that you can figure out if it's an Octoprint setting or an issue with the firmware on the board.

DFU mode is only for firmware upload and the firmware will not be running on the board when in that mode - so that won't be a help.

@capibara1 - sorry to hear your experience has not been great. I (Aus3D) haven't been selling these boards for almost a year now while I am working on the next revision. MKS and others have started shipping their own version in recent months and I have been flooded with emails requesting assistance with these boards. I am trying to answer these emails but can only spend an hour or so on them per day, which is often not enough. MKS have modified their version from my design so I have to do extra work to answer those questions. Some emails have slipped through the cracks - feel free to shoot through another email (or open an issue here) and I will try and respond as best I can.

To try and offer some guidance on compilation - I have found that recent versions of Marlin that require the STM32 HAL experience compilation errors in the Arduino IDE on Windows, and that using PlatformIO is the only option that is working for me. If you can provide specific details on the problem you're facing I can offer more guidance.

McPrince96, 2020-06-01:
@chrissbarr

i just tried it with Repetier Host and it connects to the printer (button top left is blue) but i get a timeout error.
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

@capibara1

Try Marlin Auto build in Visual studio code. Worked for me. It did stop working last week but i uninstalled Marlin Auto Build and reinstalled it and it works fine now.

https://marlinfw.org/docs/basics/auto_build_marlin.html

chrissbarr, 2020-06-01:
Hi @McPrince96,

Hmm, I'm not seeing any response from the printer firmware in the log there - it looks like Repetier Host opens the serial port, but receives no reply. Are you sure that firmware has been compiled and uploaded to the board? One way to check - Marlin should blink the orange status LED about 4 times per second after it has started running.

If Marlin is running, perhaps it is set to use the wrong serial interface - check Marlin's Configuration.h, and make sure that the serial port is set to `-1`, which is the USB interface:

`#define SERIAL_PORT -1`

McPrince96, 2020-06-01:
@chrissbarr

That did it! It works now. Thank you for the support!

McPrince96, 2020-06-01:
@chrissbarr

Not related question:
I forgot to change the jumpers on my fan 12V select and accidently sent 24V to my 12V fans. Now i don't have any output on the fan pins and the led only lights up a little. (+-50% of the other leds)
Do i have to replace the mosfets?

chrissbarr, 2020-06-01:
@McPrince96,

Glad to hear the serial comms are working!

Hmm, not sure on the MOSFET question. I would not expect them to be damaged, but it is hard to say - it depends on the failure mode of the fan to some extent.

If the 24V damaged the fan in such a way that it formed a short circuit, it could have overloaded the MOSFET. In this case, the main fuse should blow to protect the board - but it is hard to guarantee that would happen before damage occurs to the individual MOSFET.

I know some manufacturers have been changing the fuse ratings or types (or omitting them). Most are also using different MOSFETs to the ones I selected, with different characteristics that may behave differently in circumstances like this. So, the behaviour will depend a bit on the specific board you have.

Can you still get the LED to turn on or off if you try and control the fan in Repetier Host? If the LED is stuck on, then it is likely that there is some damage. Depending on how many fans/heaters you need, you can likely remap the fan to use one of the other outputs (let me know if you want info on this).

McPrince96, 2020-06-01:
@chrissbarr

The led turns on and off but at a brightness of 50% or even less compared to other leds on the board.
I changed the jumpers to 12V and coneected a new (12v) fan but it does nothing. My multimeter doesn't detect any voltage.

To be honest i got a board from banggood but it has AUS3d written on it. It is however a white board. Sorry i didn't buy one from you but last time (my previous board, rumba+) came from you) i payed almost the same order amount in taxes. Knowing i'm an expert in destroying boards this was just too expensive.

chrissbarr, 2020-06-01:
Hi @McPrince96,

No need to apologise! To be fair, I haven't had the RUMBA32 boards in stock for a long time now so even if you had wanted to grab an official one you'd have been in the same spot. Definitely hear what you're saying about taxes - sorry to hear they were so high.

Unfortunately pretty much all of the clone boards have the Aus3D branding on them - I've had more than a few people telling me in recent months that they've bought these from me, much to my confusion. MKS seems to be the exception, they have changed their board more than anyone else and have added their branding too. There's nothing wrong with anyone else making these, and I'm excited to see so many out there - just each manufacturer makes changes to components, and because they don't release a Bill of Materials I can't tell what parts they're using or what their ratings are. It makes troubleshooting issues like this tricky!

White board from Banggood - is it one of these?

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

If you remove the jumper to select 12/24V, does the LED still turn on and off? If you don't mind using that multimeter a bit more, I can suggest a few points to test.

McPrince96, 2020-06-01:
This is my board

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

The led:

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

chrissbarr, 2020-06-01:
Cool, thanks for the photos! Definitely makes it easier to see what we're talking about, cheers.

I can't see any obvious damage to the MOSFET in either image, but that doesn't say much - sometimes the damage is visible, but not always.

I'd suggest running through a few checks using your multimeter, if you'd like.

Here's an image showing the pins of the MOSFET in the same orientation as your board:

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

There's a handy guide [here](http://electronicsbeliever.com/how-to-know-if-mosfet-is-defective/) that covers a few steps to test a MOSFET. These are N-Channel (NMOS) devices that we're dealing with here. I'd suggest doing the diode test and checking the resistance between Drain and Source. All of these should be done with the power switched off, no power from USB or 24V supply etc.

Are there any of the other HE0/HE1/HE2/F0/F1 outputs that you're not using? If so, let me know which and I can check the firmware change to swap the fan to that pin if you want.

McPrince96, 2020-06-01:
I did last 2 methods. I do measure a resistance of 100k instead of 10k between gate and source.

For the last method i don't measure a continuity between drain and source. The MM stays on "1" and doesn't beep. I guess that's good, right?

I don't know how to do the first method with my MM.
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

McPrince96, 2020-06-01:
On the working mosfets i measure 1300Ohms between Drain (red) and Source (black).
I don't get this on the fan mosfets.

I do however measure around 500Ohms when measuring between Drain (black) and Source (red) on both.

chrissbarr, 2020-06-01:
Hmm. Those results would seem to suggest that the MOSFET is okay. The different resistances could be explained by the manufacturer using different parts for the heaters vs. fan MOSFETs.

It might be easier to change the fan channel in the firmware and see if the second fan MOSFET behaves the same way as the first, or if it works as expected. You could accomplish this by editing the pins file:

`Marlin/src/pins/stm32f4/pins_RUMBA32_common.h`

And swapping the FAN and FAN1 pin definitions, from:

```
#define FAN_PIN   PC9
#define FAN1_PIN  PA8
```

To:

```
#define FAN_PIN   PA8
#define FAN1_PIN  PC9
```

I've just seen this issue in the Marlin repo: https://github.com/MarlinFirmware/Marlin/issues/17519

It looks like there may be a timer conflict in the STM32 core (or Marlin's use of the timers) that clashes with the timer used for PWM on this pin. It would be worth checking if you disable PWM or use the `FAN_SOFT_PWM` feature as described in that issue, do things start working correctly?

McPrince96, 2020-06-01:
I have 2 fans and both fan channels act the same so if one is broken they're both broken. Isn't changing the 2 useless in that case?

McPrince96, 2020-06-01:
I've enabled soft pwm and now the led looks a little bit brighter but not as much as the others. The fan still doesn't spin.
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

I also have two errors but i don't think they are related.
1. "Err: EEPROm Version"
2. TMC connection error

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

chrissbarr, 2020-06-02:
Hi @McPrince96

Ah, I missed that both fans were not working - sorry, looking back now I see you said that. I thought only one fan had been plugged in at first. You are right, no point in swapping the pins then.

So it sounds like things are working with the soft PWM option now? That's great if so. I'll have to dig into why the default PWM isn't working on these pins and see if the timers can be reallocated in Marlin.

The EEPROM version error shouldn't be anything to worry about - probably just means that no EEPROM settings were found in memory. Saving the EEPROM values (M500) for the first time should clear that. Because EEPROM is emulated in flash, I believe the values will be overwritten and you'll have to do this again if you upload new firmware to the board.

The TMC connection issue sounds like it comes from the SPI defect in RUMBA32 models v1.0E and earlier. This seems to have persisted into all clone boards. If you haven't seen this yet, here are the instructions I put together on fixing this:

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

Another way of going is if you make a jumper cap that can span the right pin spacing. There's an example in https://github.com/Aus3D/RUMBA32/issues/12 of someone doing this.

McPrince96, 2020-06-02:
@chrissbarr

If i do this mod and it turns out it wasn't necessary, will there be a chance of damage?

chrissbarr, 2020-06-10:
Hi @McPrince96, just wanted to say I'm glad this mod worked and hope all is up and running now!

I'm going to mark this issue as closed now, but if there's anything else you can either leave another comment and we can reopen it, or if there's something entirely different you're welcome to open another issue.

Closed 2020-06-10.

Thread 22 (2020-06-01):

Instructions for RUMBA32 Marlin compile are obsolete

capibara1, 2020-06-01:
Hi Chris,

I created this issue based on the comments in issue #21 and issue #11

The instructions to get the board up and running with Marlin are obsolete. Here are the specifics that need to be updated:

Based on the instructions here:
 [https://github.com/Aus3D/RUMBA32/wiki/Getting-RUMBA32-Up-&-Running](https://github.com/Aus3D/RUMBA32/wiki/Getting-RUMBA32-Up-&-Running)

1. Install Arduino IDE & STM32duino Core section

Following the instructions for stm32duino used to work fine until Nov 2019. Now, whatever version of STM32 Cores that is used (access in the Arduino IDE via Tools->Board->Board Manager) from 1.6.0 to the latest 1.9.0 do not produce a successful compile. Instructions need to be updated to indicate what version of these libraries compile with specific versions of Marlin

2. The Marlin board definition instructions no longer apply to either Marlin 2.0.x or Marlin-bugfix-2.0.x. There are two versions of the RUMBA32:

Change  #define MOTHERBOARD BOARD_RAMPS_14_EFB to #define MOTHERBOARD BOARD_RUMBA32

It should now be:

Change  #define MOTHERBOARD BOARD_RAMPS_14_EFB to **#define MOTHERBOARD BOARD_RUMBA32_AUS3D**

Even with the changes in the instructions, I think using the Arduino IDE makes compiling and keeping track of all the library versions much more difficult. There should be specific instructions to set up the Platform IO environment for RUMBA32, but that's another issue.

Thanks!

chrissbarr, 2020-06-01:
Thanks @capibara1. I'll have a look at updating this shortly.

chrissbarr, 2020-06-02:
Hi @capibara1,

I haven't tried the Arduino IDE yet, as the last time I did I ran into a few problems, but I've confirmed that the following PlatformIO setup works for me:

1. Using VSCode with PlatformIO installed (other IDEs are probably similar, but I have not tried).
2. Download/clone Marlin 2.0.x (see below for notes on version) and open it in VSCode.
3. Edit the configuration.h file with the minimum necessary changes:

```
107: #define SERIAL_PORT -1

130: #ifndef MOTHERBOARD
131:   #define MOTHERBOARD BOARD_RUMBA32_AUS3D
132: #endif

409: #define TEMP_SENSOR_0 998 // not necessary, but so I could test without a thermistor
```

4. Locate the `env:rumba32_f446ve` folder in the `Project Tasks` window, and expand it:

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

5. Click on `Build` in the `env:rumba32_f446ve` folder. You should see a few success messages once the process completes:

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

6. Connect RUMBA32 to the USB port. Reset the RUMBA32 board by holding BOOT0, pressing RESET, then releasing BOOT0. The LED should blink once when you do this. Device manager should show the board as so:

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

7. Click on `Upload` in the `env:rumba32_f446ve` folder. Again, you should see a few success messages once the process completes:

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

Here's the full output I get when building/uploading:

<details>
  <summary>Full Output (Click to Expand)</summary>

```
> Executing task in folder Marlin: C:\Users\Chris\.platformio\penv\Scripts\platformio.exe run --target upload --environment rumba32_f446ve <

Processing rumba32_f446ve (platform: ststm32; board: rumba32_f446ve; framework: arduino)
---------------------------------------------------------------------------------------------------------------------------------------------------------------------------------------------------------------------------------Verbose mode can be enabled via `-v, --verbose` option
CONFIGURATION: https://docs.platformio.org/page/boards/ststm32/rumba32_f446ve.html
PLATFORM: ST STM32 6.1.0 > 3D Printer control board
HARDWARE: STM32F446RET6 180MHz, 128KB RAM, 512KB Flash
DEBUG: Current (blackmagic) External (blackmagic, jlink, stlink)
PACKAGES:
 - framework-arduinoststm32 4.10800.200207 (1.8.0)
 - tool-dfuutil 1.9.200310
 - tool-openocd 2.1000.190707 (10.0)
 - tool-stm32duino 1.0.2
 - toolchain-gccarmnoneeabi 1.90201.191206 (9.2.1)
Converting Marlin.ino
LDF: Library Dependency Finder -> http://bit.ly/configure-pio-ldf
LDF Modes: Finder ~ chain, Compatibility ~ soft
Found 20 compatible libraries
Scanning dependencies...
Dependency Graph
|-- <LiquidCrystal> 1.5.0
|   |-- <Wire> 1.0
|-- <TMCStepper> 0.6.2
|   |-- <SoftwareSerial> 1.0
|   |-- <SPI> 1.0
|-- <U8glib-HAL> 0.4.1
|   |-- <Wire> 1.0
|   |-- <SPI> 1.0
|-- <Adafruit MAX31865 library> 1.0.3
|   |-- <SPI> 1.0
|-- <LiquidTWI2>
|   |-- <Wire> 1.0
|-- <Arduino-L6470> 0.8.0
|-- <SailfishLCD>
|-- <SailfishRGB_LED>
|   |-- <Wire> 1.0
|-- <SlowSoftI2CMaster>
|-- <SPI> 1.0
|-- <Servo> 1.1.2
|-- <IWatchdog> 1.0.0
|-- <Wire> 1.0
Building in release mode
Checking size .pio\build\rumba32_f446ve\firmware.elf
Advanced Memory Usage is available via "PlatformIO Home > Project Inspect"
RAM:   [=         ]   5.3% (used 6980 bytes from 131072 bytes)
Flash: [==        ]  16.2% (used 84848 bytes from 524288 bytes)
Configuring upload protocol...
AVAILABLE: blackmagic, dfu, jlink, serial, stlink
CURRENT: upload_protocol = dfu
Uploading .pio\build\rumba32_f446ve\firmware.bin
dfu-util 0.9

Copyright 2005-2009 Weston Schmidt, Harald Welte and OpenMoko Inc.
Copyright 2010-2020 Tormod Volden and Stefan Schmidt
This program is Free Software and has ABSOLUTELY NO WARRANTY
Please report bugs to http://sourceforge.net/p/dfu-util/tickets/

Match vendor ID from file: 0483
Match product ID from file: df11
Opening DFU capable USB device...
ID 0483:df11
Run-time device DFU version 011a
Claiming USB DFU Interface...
Setting Alternate Setting #0 ...
Determining device status: state = dfuERROR, status = 10
dfuERROR, clearing status
Determining device status: state = dfuIDLE, status = 0
dfuIDLE, continuing
DFU mode device DFU version 011a
Device returned transfer size 2048
DfuSe interface name: "Internal Flash  "
Downloading to address = 0x08000000, size = 85364

Erase           [                         ]   0%            0 bytes
Erase           [=                        ]   4%         4096 bytes
Erase           [==                       ]   9%         8192 bytes
Erase           [===                      ]  14%        12288 bytes
Erase           [====                     ]  16%        14336 bytes
Erase           [=====                    ]  21%        18432 bytes
Erase           [======                   ]  26%        22528 bytes
Erase           [=======                  ]  28%        24576 bytes
Erase           [========                 ]  33%        28672 bytes
Erase           [=========                ]  38%        32768 bytes
Erase           [==========               ]  40%        34816 bytes
Erase           [===========              ]  45%        38912 bytes
Erase           [============             ]  50%        43008 bytes
Erase           [=============            ]  52%        45056 bytes
Erase           [==============           ]  57%        49152 bytes
Erase           [===============          ]  62%        53248 bytes
Erase           [================         ]  64%        55296 bytes
Erase           [=================        ]  69%        59392 bytes
Erase           [==================       ]  74%        63488 bytes
Erase           [===================      ]  76%        65536 bytes
Erase           [====================     ]  81%        69632 bytes
Erase           [=====================    ]  86%        73728 bytes
Erase           [======================   ]  88%        75776 bytes
Erase           [=======================  ]  93%        79872 bytes
Erase           [======================== ]  98%        83968 bytes
Download        [                         ]   0%            0 bytes
Download        [=                        ]   4%         4096 bytes
Download        [=                        ]   7%         6144 bytes
Download        [==                       ]   9%         8192 bytes
Download        [===                      ]  14%        12288 bytes
Download        [====                     ]  16%        14336 bytes
Download        [=====                    ]  21%        18432 bytes
Download        [======                   ]  26%        22528 bytes
Download        [=======                  ]  28%        24576 bytes
Download        [========                 ]  33%        28672 bytes
Download        [=========                ]  38%        32768 bytes
Download        [==========               ]  40%        34816 bytes
Download        [===========              ]  45%        38912 bytes
Download        [============             ]  50%        43008 bytes
Download        [=============            ]  52%        45056 bytes
Download        [==============           ]  57%        49152 bytes
Download        [==============           ]  59%        51200 bytes
Download        [===============          ]  62%        53248 bytes
Download        [================         ]  64%        55296 bytes
Download        [=================        ]  69%        59392 bytes
Download        [==================       ]  74%        63488 bytes
Download        [===================      ]  76%        65536 bytes
Download        [====================     ]  81%        69632 bytes
Download        [=====================    ]  86%        73728 bytes
Download        [======================   ]  88%        75776 bytes
Download        [======================   ]  91%        77824 bytes
Download        [=======================  ]  93%        79872 bytes
Download        [======================== ]  98%        83968 bytes
Download        [=========================] 100%        85364 bytes
Download done.
File downloaded successfully
Transitioning to dfuMANIFEST state
================================================================================================= [SUCCESS] Took 25.50 seconds =================================================================================================
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
capibara1, 2020-06-02:
See comments here: [Issue #24] (https://github.com/Aus3D/RUMBA32/issues/24#issuecomment-637230802)

chrissbarr, 2020-07-07:
I've updated the [wiki](https://github.com/Aus3D/RUMBA32/wiki) with instructions using PlatformIO, based on our conversations here and some changes that have been pulled into Marlin since. These instructions are currently up to date - hopefully that stays the case for a while!

Closed 2020-07-07.

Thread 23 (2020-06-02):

[FAQ] SPI Stepper Driver Defect

chrissbarr, 2020-06-02:
The purpose of this issue is to put info on this problem in one place for easy reference.

As has been discussed in several issues in this repository and others, there is a design defect with the SPI pinout in the stepper driver sockets that prevents bidirectional SPI communication with stepper drivers from working properly. Because of this, SPI support for stepper drivers in Marlin and other firmware does not work correctly.

This issue is present on all board versions from v1.0A to v1.0E. For reference, v1.0E is the only revision sold by Aus3D (the earlier revisions were only used for internal development). I have seen some vendors selling clones based on v1.0D, so I am trying to cover my bases by describing all models, whether they have been sold by Aus3D or not.

At the moment, all clone boards from other vendors seem to be based on either v1.0D or v1.0E, and this issue is present in all those boards that I have seen. This includes MKS's modified RUMBA32 board (currently v1.0), which looks to be derived from v1.0E.

If you want to get SPI-based drivers working, the following instructions describe one method:

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

MKS describes a slightly different method in their FAQ [here](https://github.com/makerbase-mks/MKS-RUMBA32/wiki/About-RUMBA32-TMC-SPI-%22CONNECTION-ERROR%22-FAQ), in which the SLP and RST pins are soldered together. This should get the SPI signals to the correct pins, but it also puts one of the signals on another pin - whether or not all models of stepper driver will work correctly with this is unclear to me.

chrissbarr, 2020-06-02:
### Other discussions on this issue:
First discussed in this issue: https://github.com/Aus3D/RUMBA32/issues/12#issuecomment-536172666
Discussed in MKS RUMBA32 issues here: https://github.com/makerbase-mks/MKS-RUMBA32/issues/2

studiodyne, 2021-01-28:
Hi , may be i can suggest something .... You have to redraw the new board , may you can add some features ...
I give you all my ideas , may be some will interest you , and after reading this , you can delete , if you want to keep secret these ideas
1-) Create a new expanion port with   all ' step + dir ' pins , that will make 12 gpios available when using SPI drivers only ,  this new port give infinite possibilities , add 12 motors , or servos or alarm pins or robotics pins or anything else
2-) Create a 6v power for servos , because , the 5v works only on very short cables , but when using long cables , the servos don't want to work because of too low voltage
3-) Add 2 jumpers , for the EEPROM for users that want more PROGMEM , or prefer EEPROM , or ' like  me ' that want the 2 free pins of the i2c bus
4-) create a three pins dedicated bltouch port , i know it's risked if one day a new firmware breaks something in the timers and pins ,that breaks bltouch pwm , but for the moment it's works fine on pb8/pb9/pd15 and others
5-) add MKS tft connector on the same sw uart pins
6-) big connector for heaters , same as power supply because ' super volcano 80w and i'm sure , very soon a new ultra volcano 150w ' , the mosfet can drive , but connectors .... not sure that have the size of the cable
7-) another type of buttons , because , resetting and bootloading is not easy

Thks for your job

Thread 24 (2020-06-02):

Board does not run with Marlin 2.0 PlatformIO compile

capibara1, 2020-06-02:
I am trying to do the following without success:

1. Compile Marlin-2.0.x
2. Upload it to the board
3. Have the board do its usual reset and start running Marling.

### Marlin setup

Marlin versions affected:
Marlin-2.0.x (currently 2.0.5.3)

Marlin configurations:
These are the only Configuration.h changes that I am making to keep the process simpler:

#define SERIAL_PORT = -1
**#define MOTHERBOARD BOARD_RUMBA32_AUS3D**
#define DEFAULT_NOMINAL_FILAMENT_DIA 1.75
#define X_DRIVER_TYPE A4988
#define Y_DRIVER_TYPE A4988
#define Z_DRIVER_TYPE A4988
#define E0_DRIVER_TYPE A4988

Configuration_adv.h not changed at all

### Compilation Issues

1. First compile issue: Arduino IDE compile is impossible. It fails with any version of STM32duino (1.9.0). Abandoned this approach for PlatformIO. I hope instructions for future users are updated to encourage include PlatformIO. Issue #22.

2. Marlin platformio.ini file for RUMBA32 is incorrect. It needs to be changed (Issue #21, Issue #11 )
This is what the Marlin platformio.ini has for BOARD_RUMBA_32_AUS3D (with annotated changes/questions):

[env:rumba32_f446ve]
platform      = ststm32
board         = rumba32_f446ve
build_flags   = ${common.build_flags}
  -DSTM32F4xx
  -DARDUINO_RUMBA32_F446VE
  -DARDUINO_ARCH_STM32
  "-DBOARD_NAME=\"RUMBA32_F446VE\""
  -DSTM32F446xx
  -DUSBCON
  **-DUSBD_VID=0x0483  --> CORRECT? (See [here](https://github.com/MarlinFirmware/Marlin/pull/16202#issuecomment-565669256) RUMBA MKS board uses 0x8000. It compiles with either value, but what is the correct one and does it matter?)**
  "-DUSB_MANUFACTURER=\"Unknown\""
  "-DUSB_PRODUCT=\"RUMBA32_F446VE\""
  -DHAL_PCD_MODULE_ENABLED
  -DUSBD_USE_CDC
  -DDISABLE_GENERIC_SERIALUSB
  -DHAL_UART_MODULE_ENABLED
  -Os
lib_ignore    = Adafruit NeoPixel
**src_filter    = ${common.default_src_filter} +<src/HAL/STM32>  --> MISSING ENTRIES absolutely needed to compile: +<src/HAL/STM32_F4_F7> -<src/HAL/STM32_F4_F7/STM32F7> **
** monitor_speed = 500000 --> Should this be 250000 ? **
upload_protocol = dfu
**lib_deps      = ${common.lib_deps} --> MISSING (See [here](https://github.com/MarlinFirmware/Marlin/pull/16202#issuecomment-565669256) and issue #11  )**

Modifying the platformio.ini file compiles successfully, however:

### Uploading and Running (or not)

With the platformio.ini setting for upload_protocol=dfu, the compiler attaches a dfu suffix to the firmware.bin file:
Advanced Memory Usage is available via "PlatformIO Home > Project Inspect"
RAM:   [=         ]   5.4% (used 7060 bytes from 131072 bytes)
Flash: [==        ]  17.4% (used 91124 bytes from 524288 bytes)
**Adding dfu suffix to firmware.bin**
**dfu-suffix (dfu-util) 0.9**

Copyright 2011-2012 Stefan Schmidt, 2013-2014 Tormod Volden
This program is Free Software and has ABSOLUTELY NO WARRANTY
Please report bugs to http://sourceforge.net/p/dfu-util/tickets/

**Suffix successfully added to file**

And it can be uploaded to the RUMBA32 (in Bootloader mode). It uploads successfully:

Configuring upload protocol...
AVAILABLE: blackmagic, dfu, jlink, serial, stlink
CURRENT: upload_protocol = dfu
Uploading .pio/build/rumba32_f446ve/firmware.bin
dfu-util 0.9

Copyright 2005-2009 Weston Schmidt, Harald Welte and OpenMoko Inc.
Copyright 2010-2020 Tormod Volden and Stefan Schmidt
This program is Free Software and has ABSOLUTELY NO WARRANTY
Please report bugs to http://sourceforge.net/p/dfu-util/tickets/

Match vendor ID from file: 0483
Match product ID from file: df11
Opening DFU capable USB device...
ID 0483:df11
Run-time device DFU version 011a
Claiming USB DFU Interface...
Setting Alternate Setting #0 ...
Determining device status: state = dfuERROR, status = 10
dfuERROR, clearing status
Determining device status: state = dfuIDLE, status = 0
dfuIDLE, continuing
DFU mode device DFU version 011a
Device returned transfer size 2048
DfuSe interface name: "Internal Flash  "
Downloading to address = 0x08000000, size = 91644
Download        [=========================] 100%        91644 bytes
Download done.
File downloaded successfully
Transitioning to dfuMANIFEST state

After successful compile I expect the board to reset and start running the program But then the board does not restart. The orange LED1 does not flash at all and there is no way to get the board to start running Marlin.
Doing an lsu's (MacOS), I can see the board is connected in "FS mode". I don't know what that is but there is no communication with the board via host software (Pronterface).

Bus 020 Device 025: ID 0483:5740 STMicroelectronics RUMBA32_F446VE CDC in FS Mode  Serial: 376933553337

I don't know what else to try at this point. I am very frustrated with this. For now, my board is bricked. Any help is appreciated.

chrissbarr, 2020-06-02:
Hi @capibara1, sorry to hear this isn't working. Please check the PlatformIO instructions I've just posted in the other issue (https://github.com/Aus3D/RUMBA32/issues/22#issuecomment-637216106) and see if they work for you. I did not have to modify the platformio.ini file for this to work.

capibara1, 2020-06-02:
HI Chris,
I appreciate the instructions. Hopefully the will become the default instructions in the "Getting RUMBA32 Up and Running page" instead of buried in a GitHub issue thread.

I was just able to compile the master branch of Marlin 2.0.x (tag 2.0.5.3) by using and modifying the platform.ini file from the bug fix branch:

1. git clone https://github.com/MarlinFirmware/Marlin.git
2. git clone -branch bugfix-2.0.x https://github.com/MarlinFirmware/Marlin.git
3. cp Marlin-bugfix-2.0.x/platformio.ini Marlin/.
4. Edit Marlin/platformio.ini:

Replace:

src_filter    = ${common.default_src_filter} +<src/HAL/STM32>

with

src_filter    = ${common.default_src_filter} +<src/HAL/STM32> +<src/HAL/STM32_F4_F7> -<src/HAL/STM32_F4_F7/STM32F7>

That compiled and uploaded completely (with a few warnings, see log below). Now I can finally connect to the board!

Next, I will attempt the compile with the full Marlin configuration files. I will update what I find.

Thank you!

capibara1, 2020-06-02:
@chrissbarr
Yes, I can compile the master branch 2.0.x with full configuration and that platformio.ini modification explained above but the fans don't work at all, the LCD screen is totally garbled and there is an error message that was reported in issue #21 : **Err: EEPROM Version.**

The bugfix-2.0.x version compiles and uploads without modifications to the platformio.ini and the printer shows the correct message "AUS3D RUMBA32 Ready" but the LCD screen is still garbled, and fans still don't work at all (FAN onboard LED lights up but fan doesn't spin).  So the printer is not useable at all.

The LCD issue may have something to do with the LiquidCrystal 1.5.0 library. See compile warnings in the attached file. The fans, I will have to look back at issue #21 but I don't think there was a resolution to the issue (fans did not end up spinning)

What do you suggest as a next step?

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

[LCD_compile_warnings.txt](https://github.com/Aus3D/RUMBA32/files/4714834/LCD_compile_warnings.txt)

chrissbarr, 2020-06-02:
Hi @capibara1,

I believe the resolution to the fans issue in https://github.com/Aus3D/RUMBA32/issues/21 was successful - @McPrince96 added an edit to his message stating that the fans were working (see https://github.com/Aus3D/RUMBA32/issues/21#issuecomment-636879642). The fix here was to use the soft PWM feature in Marlin (`#define FAN_SOFT_PWM`). I've also tested this on my board here and it is working for me. It would be better to have the hardware PWM working, but until the underlying issue is found and corrected the soft PWM should be a very usable solution. You can experiment with the options for frequency and dithering if you'd like.

I am not clear on why the platformio.ini modification was needed. Were you getting some error without this?

I think including the `<src/HAL/STM32_F4_F7>` will cause you trouble, as the HAL described in those folders uses an entirely different Arduino Core - it targets the older STM32Generic Arduino Core, whereas RUMBA32 support in Marlin uses the official STM32Duino Core, which is targeted in the `<src/HAL/STM32>` folder. I do not know what effect including both would have - hopefully, the `#ifdef` guards in the HAL headers will make it so that only one of the HALs is used, preferably the one that supports RUMBA32. I can't guarantee that this is what is happening though, so I would advise against including these extra folders.

I've seen the LCD issue before - I believe that is a result of timing problem coming from the faster microcontroller, where the original code was built around the slower 8-bit devices. Testing with a display I have on hand, I see the same thing. Adding these lines to the end of the Configuration.h file solves it for me:
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
chrissbarr, 2020-06-02:
On the EEPROM error - that should go away once you have saved values to EEPROM (M500) once. You may need to do an M502 (settings reset) first - I'm unsure. If that doesn't do it, let me know and I'll check further.

chrissbarr, 2020-06-02:
I've just been having a look at the Marlin troubleshooting docs. I see they touch on this EEPROM error [here](https://marlinfw.org/docs/basics/troubleshooting.html#eeprom-errors), and that seems to confirm that an M502 followed by an M500 should initialise the EEPROM as required.

The LCD problem [is also discussed](https://marlinfw.org/docs/basics/troubleshooting.html#graphical-lcd-artifacts) and the same solution of adding the above delays is suggested, though with different values. I've had these delays kicking around for a while and am not sure where I first came across them - so I'm not sure if there's any significance in the different values. The ones above have worked for me - if they don't do the trick for you, maybe try the delays given in the Marlin docs instead.

capibara1, 2020-06-02:
Thanks Chris,

Finally everything (compile/upload/run) is working now for the AUS3D RUMBA32, at least for the bugfix-2.0.x Marlin release.
Combination that works for other's benefit:

- Marlin-bugfix-2.0.x (This specific [commit](https://github.com/MarlinFirmware/Marlin/pull/16082))
- Compile using VSCode with PlatformIO - Arduino IDE method does not work.
- platformio.ini - Default that comes with Marlin, no changes
- Configuration.h
  * `#define MOTHERBOARD BOARD_RUMBA32_AUS3D`
  * `#define SERIAL_PORT -1`
  * Fan PWM workaround (or fans won't start): `#define FAN_SOFT_PWM`
  * LCD (this was my specific screen issue for RepRap Discount Full Graphic Display, delay values may be different for others):
 ```
  #define ST7920_DELAY_1 DELAY_NS(200)
  #define ST7920_DELAY_2 DELAY_NS(350)
  #define ST7920_DELAY_3 DELAY_NS(200)
```
- EEPROM error may or may not show up (is intermittent for me): Just execute M502, M500 after connecting to host software. Should always do this when new firmware is uploaded anyways.

chrissbarr, 2020-06-03:
That's great news @capibara1, glad to hear it!

Thanks for noting the info/configuration that has worked for you, that's a big help and will be useful to others I am sure.

I will amend the documentation shortly to use the PlatformIO method, rather than the Arduino IDE method.

I'll close this issue now, but if you run into more trouble with this feel free to leave a comment and we will reopen it (or open a new issue - whatever you prefer).

capibara1, 2020-06-03:
I appreciate the help Chris!

Note: the "EEPROM Version Error. Initialize EEPROM?" shows up every time after reset, even if M502/M500 are executed. When M501 (Restore settings from EEPROM) is executed, you still get the "EEPROM version mismatch (EEPROM= Marlin=V79)"

How can we eventually have the RUMBA32 compile out of the master Marlin-2.0.x branch? It seems that it perpetually and only works with the bug fix branch and that is not great for stability.

Thanks again.

Closed 2020-06-03.

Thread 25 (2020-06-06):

jumpers to set for DRV8825 drivers

phongshader, 2020-06-06:
I don't see any documentation on how to set the jumpers for the drivers. If I want to set up x and y drivers to 16 micro steps and z to 32 micro steps. SLP MS3 MS2 MS1 or maybe I don't understand how this works. Documentation?

3dlpm, 2020-06-07:
@phongshader I actually recommend that you don't use DRV8825 drivers for your 3d printer at all. They are bad for reasons explained:
1. Here: [https://forum.pololu.com/t/poor-drv8825-microstepping-performance/15266](https://forum.pololu.com/t/poor-drv8825-microstepping-performance/15266)

2. And here (look at the links in the "External notes/references" section) : [https://reprap.org/wiki/DRV8825](https://reprap.org/wiki/DRV8825)

A4988 stepper drivers are proven to be better to use for 3D printers than the DRV8825.
Another alternative, if you want silent operation and to be able to control currents and other parameters via the built-in RUMBA32 SPI interface, you want to use TMC2130 or TMC5160 drivers which are SPI controllable. I know the RUMBA32 definitely supports TMC2130s but not sure if it supports the higher currents driven by the TMC5160.

In any case, for DRV8825 the jumper settings are in the picture below. They are in the RUMBA32 schematic in this GitHub page and you can also do a search on DRV8225 pinout.

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

phongshader, 2020-06-08:
Thank you, I will be changing over to TMC5160 drivers. I'm upgrading from a rumba to rumba32 and I want to tackle one issue at a time, switch the board with the drivers I have that I know will work with this board, get it running , then switch the drivers that have their own set of problems with this board

Closed 2020-06-09.

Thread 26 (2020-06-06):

Fan PWM Troubleshooting / Timer Investigation

chrissbarr, 2020-06-06:
Collecting information for troubleshooting why PWM on FAN (PC9) isn't outputting the expected values when running Marlin bugfix-2.0.x.

Suspect there is a conflict somewhere / the same timer is being used in multiple places or something to that effect.

## Timers in use
Checking everywhere timers are configured/selected.
### STM32 Arduino Core
[RUMBA32_F446VE/variant.h](https://github.com/stm32duino/Arduino_Core_STM32/blob/master/variants/RUMBA32_F446VE/variant.h):
```
// Timer Definitions
// Use TIM6/TIM7 when possible as servo and tone don't need GPIO output pin
#define TIMER_TONE              TIM6
#define TIMER_SERVO             TIM7
```
[SoftwareSerial/src/SoftwareSerial.cpp](https://github.com/stm32duino/Arduino_Core_STM32/blob/master/libraries/SoftwareSerial/src/SoftwareSerial.cpp)
```
// It's best to define TIMER_SERIAL in variant.h. If not defined, we choose one here
// The order is based on (lack of) features and compare channels, we choose the simplest available
// because we only need an update interrupt
#if !defined(TIMER_SERIAL)
  #if defined (TIM18_BASE)
    #define TIMER_SERIAL TIM18
  #elif defined (TIM7_BASE)
    #define TIMER_SERIAL TIM7
  #elif defined (TIM6_BASE)
    #define TIMER_SERIAL TIM6
  #elif defined (TIM22_BASE)
    #define TIMER_SERIAL TIM22
```
### Marlin
[STM32/timers.cpp](https://github.com/MarlinFirmware/Marlin/blob/bugfix-2.0.x/Marlin/src/HAL/STM32/timers.cpp):
```
#elif defined(STM32F401xC) || defined(STM32F401xE)
  #define HAL_TIMER_RATE (F_CPU / 2)
  #define MCU_STEP_TIMER  9
  #define MCU_TEMP_TIMER 10
#elif defined(STM32F4xx) || defined(STM32F7xx)
  #define HAL_TIMER_RATE (F_CPU / 2)
  #define MCU_STEP_TIMER  6           // STM32F401 has no TIM6, TIM7, or TIM8
  #define MCU_TEMP_TIMER 14           // TIM7 is consumed by Software Serial if used.
#endif
```

## Timers Reference
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

phongshader, 2020-06-08:
I don't know if the issue I'm having is connected to this but it sounds like it is. If I run a m106 command FAN0 does not turn on however FAN0 led does light up. The voltage at the fan terminal after a m106 s255 is 1.39 and s128 is .93, s0 is .10

chrissbarr, 2020-06-08:
Hi @phongshader,

The problem you're describing is the reason I started looking into this. However, I've found the fan issue is not related to any of the above, but is an issue with the PWM frequency+resolution in 1.7.0 of the Arduino Core (which is the version ProjectIO + Marlin currently uses). When ProjectIO and Marlin update to use v1.9 this issue should be fixed.

In the meantime, the best way to get fans running correctly is to use Marlin's `#define FAN_SOFT_PWM` feature - all fans should work when that is enabled.

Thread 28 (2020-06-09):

dfu mode device not recognized

phongshader, 2020-06-09:
mac:
FS mode
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

dfu mode
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

Win 10
VCP_V1.5.0_Setup_W8_x64_64bits.exe installed, it recognized the board worked once to get firmware onto board but I can no longer update the firmware.
FS mode:
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

dfu mode
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

no STM32 bootloader.
Is there a way to load firmware without dfu?

platformio:
`Uploading .pio/build/rumba32_mks/firmware.bin
dfu-util 0.9

Copyright 2005-2009 Weston Schmidt, Harald Welte and OpenMoko Inc.
Copyright 2010-2020 Tormod Volden and Stefan Schmidt
This program is Free Software and has ABSOLUTELY NO WARRANTY
Please report bugs to http://sourceforge.net/p/dfu-util/tickets/

Match vendor ID from file: 0483
Match product ID from file: df11
dfu-util: No DFU capable USB device available
*** [upload] Error 74`

chrissbarr, 2020-06-09:
Hi @phongshader,

Hmm, in the images the board is recognised and connected, but not in DFU mode. At the moment DFU mode has to be entered manually by pressing the buttons on the board - are you doing this? Refer to the instructions (from [here](https://github.com/Aus3D/RUMBA32/wiki/Uploading-Sketch#method-1-upload-via-usb-dfu)):

1. Press and hold RUMBA32 BOOT button.
2. Press and release RUMBA32 RESET button.
3. Release RUMBA32 BOOT button.
4. RUMBA32 is now in hardware bootloader mode and will accept firmware upload via USB DFU.

The orange LED on the board should flash once when you do the above (approximately after RESET is released). This indicates the board is in DFU mode and has a working USB connection. You should be able to see the device in device manager as so:

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

I'm not sure if you've seen the troubleshooting steps here: https://github.com/Aus3D/RUMBA32/wiki/Uploading-Sketch#troubleshooting

That CDC FS mode comes up shows that the USB connection is working correctly and the hardware is functioning correctly. CDC FS mode is the serial mode that the board enters when running user code. USB DFU is a different mode that is controlled by the hardware bootloader - the good news is that the DFU bootloader is built in and can not be erased/overwritten/removed. I would make sure that you are pressing the buttons firmly, in the correct order, and watch for the orange LED to make sure that the board is entering DFU mode.

phongshader, 2020-06-09:
I did indeed press boot and reset to get into dfu mode. The board does connect until I hold the boot button and press and release the reset button then it disappears from the device manager. I will check to see if the led, led1?,  flashes once when the reset button is released.
The only way to load firmware, other than dfu, is with a usb to serial adapter?

chrissbarr, 2020-06-09:
Hi @phongshader,

The behaviour you are describing sounds fairly normal. The device should disappear from device manager when you press RESET, as resetting will disconnect it. It should reappear within a second or two of RESET being released, but may be under a different heading in device manager - for me, USB DFU ("STM32 BOOTLOADER") shows up under "Universal Serial Bus devices", whereas when it is in normal mode it shows up under "Ports (COM & LPT)".

LED1 is the correct place to be looking. For me, it flashes for about 1/4 of a second after releasing RESET. I believe the LED lights when starting the bootloader, and turns off when the USB connection with the host computer is opened correctly. The exact timing _might_ vary slightly depending on the host PC / OS (I'm unsure if there can be differences in how quickly devices are enumerated etc.), but it should be a short flash that last some part of a second. If you try to enter the bootloader without the USB cable connected, the LED will stay lit for some time (> 60s) before it times out and stops trying to open the connection. If you see the LED staying lit that would indicate some connection problem - but the fact that it shows up when in CDC mode makes me think the connection is physically good.

There's no harm in holding BOOT down longer than needed, and there's no real timing requirement - as long as BOOT is held down when RESET is released, it should enter bootloader mode.

### Upload Methods
There are a few methods, but the USB DFU method should be the simplest and it's the only one I use regularly. It's also the only one that doesn't require any extra hardware. Upload methods currently supported in the Arduino IDE are:

- STM32CubeProgrammer (SWD)
  - Serial Wire Debug (SWD) is the dedicated programming/debugging interface for the MCU and can be used for debugging purposes as well as uploading etc.
  - It requires a dedicated programmer such as the ST-Link V1/V2/V3 or similar. Adafruit carry one here: https://www.adafruit.com/product/2548
  - There are generic models on Aliexpress etc for a few dollars. I bought two at one stage and had one of them not work, so it may be a bit of a buyer-beware thing.
- STM32CubeProgrammer (Serial)
  - Program the MCU using the integrated bootloader via the serial U(S)ART interface. You need a 3.3V-compatible USB-Serial adaptor to do this, to be wired as shown in the wiki image:
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
- STM32CubeProgrammer (DFU)
  - Program the MCU using the integrated bootloader via the USB DFU interface.

I have used SWD programmers on other boards, but have not had to use them on RUMBA32. I have only used the Serial upload method once on these boards, to confirm I had the instructions correct when I was writing that wiki page. Both the USB DFU and Serial methods require the board to be in bootloader mode, so if you can make Serial work then DFU should work anyway.

phongshader, 2020-06-09:
I pulled out an ooold win7 netbook and it recognized the board in dfu mode. I was able to load firmware...it took several hours to compile. After that I was able to connect using a newer laptop. I don't know what happened but it doesn't seem to be a board issue

Closed 2020-06-09.

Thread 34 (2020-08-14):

Entering DFU mode problem

JoeScotty, 2020-08-14:
Purchased a Aus3D Rumba32 V1.03e and suddenly having a problem entering the DFU mode.
The way it worked up to now:
plug in USB, press and hold BOOT, press and release RESET, finally release BOOT. The LED1 flashes once.
I can follow the process on Win10 device manager, COMx is dropped and STM32 Bootloader came up.

Without an obvious change, the LED1 does not flash any more and the changes in the device manager did not happen any more.

Tried to find solutions. There was one hint with the quartz frequency being out of tolerance, which could cause such a problem.
Would be happy getting some hints (others than dropping the board ;-).
Thanks!

chrissbarr, 2020-08-15:
Hi @JoeScotty. Sorry to hear you've run into a bit of trouble. Happy to help troubleshoot if I can!

To confirm, is it V1.0E that you have?

I'm not familiar with any issues impacting the ceramic resonator on the board - it might be possible, but it's not something I've seen before. Importantly, I believe the resonator isn't used for the DFU bootloader's USB communication (as the bootloader runs before the clock inputs are initialised in the firmware). My understanding is that the USB DFU comms use the internal clock source, and does some trimming of that based on the USB timing frames. I am not very familiar with the process - but I believe it is fairly resilient to issues with the resonator on the board.

There is a recently-noticed flaw in the design that can impact the bootloader correctly starting. There is a pull-down resistor required on pin PB2 that is not included on boards prior to V1.1B. This can result in intermittent bootloader behaviour in some cases - if PB2 floats high, that can prevent the bootloader from running in the correct mode.

PB2 is broken out to the EXP2 header, and so can be affected by things attached to that header (commonly displays etc.). It is possible that an issue with this pin is causing your trouble.

If you are handy with a soldering iron, the easiest fix is to add in a 100K resistor between PB2 and GND. There is no downside in the regular use of the board in adding this resistor - this is what is being done on V1.1B forward. This can be done on the back of the board like so:

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

Otherwise, there are some soldering-free ways we can check if this is the problem. If you have any female jumper wires you can temporarily connect PB2 directly to GND. The only downside to this is that it prevents using any peripheral attached to the EXP2 header. However, it might be an easy way to check if this is the problem you're seeing.

It's possible that it is a different issue that you're seeing. At the moment, this is the only issue I'm aware of surrounding the bootloader - so I'd suggest checking if the above solves the issue, and if not we can explore other options.

Let me know what you think, happy to explain anything more or do anything else I can to help.

JoeScotty, 2020-08-15:
Hi Chris,
thanks for your quick reply!
I  tested adding the 100k with clips and entering the DFU mode worked in all tests!
So I'm very sure this was the solution.
I'm going to solder the resitor like you suggested.

May I suggest to add this mod to the SLI mod already published for the V1.0E.

Now I'm happy that I can proceed with firmware configuration!
Thanks again, Regards
JoeScotty

Closed 2020-08-15.

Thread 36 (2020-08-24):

build failed with Arduino

19504643, 2020-08-24:
I'm using marlin bugfix-2.0.x branch, following the setup https://github.com/Aus3D/RUMBA32/wiki/Getting-RUMBA32-Up-&-Running#arduino-setup
first I got the board config error:
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
I changed `BOARD_RUMBA32` to `BOARD_RUMBA32_V1_0`

then I got errors:

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

chrissbarr, 2020-08-24:
Hi @19504643,

In my experience, there have been issues using the Arduino IDE to compile Marlin 2.0 for STM32 boards for a while. I recommend using PlatformIO, as documented here:

https://github.com/Aus3D/RUMBA32/wiki/Marlin---Build-and-Upload-(PlatformIO)

I am not sure if your issues relate to this or not - but when I last tried, I was not able to get a successful compilation out of the IDE at all, even after all other errors were resolved. So, it's something I would recommend in general if convenient.

You are correct to have changed the board define. This is better captured on the above page, along with the info page here:

https://github.com/Aus3D/RUMBA32/wiki/Recommended-Marlin-Configuration

The instructions on configuring for the Arduino IDE are a little out of date at this stage, hence the wrong board definition.

The error that you are seeing seems to relate to the way timers are handled. Timer handling errors often relate to having the wrong version of the STM32duino Core installed (my understanding is that Marlin currently needs a slightly older version - not the latest - installed). I believe it is 1.7.0 that is needed but am not sure. PlatformIO grabs the specific version needed automatically, another reason I would recommend going that route.

I would suggest checking which version of the STM32Duino Core is installed, and changing it to v1.7.0 if possible. Otherwise, swapping over to use PlatformIO should resolve this issue automatically.

Let me know if you're still stuck, happy to look into it more.

19504643, 2020-10-12:
ok, I change back the STM32Duino Core to v1.7.0 and it works, finally I get the bin file, and flash it to the board
the LED1 is blinking, and I install the virtual comport driver, then I found the STMicroelectronics Virtual COM Port (COM10) in device manager, I open it with baudrate 250000 or 115200 in debug monitor, but it seems not working with nothing produced when it startup or I send any gcode, what's the problem

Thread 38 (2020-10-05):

Can't connect a MKS Rumba32 board via USB

Bernouillle, 2020-10-05:
Hello there!
I know, that the MKS Rumba32 board is not sold by your company, but maybe you can help me to solve my connection problem. I'm using Klipper as the firmware, where a Raspberry Pi is used as a host computer to do all the calculations and to communicate with the Rumba32 board. Unfortunately i am not able to find the USB connection of the Rumba32 board with the Raspberry. Do you have an idea how to fix this problem?
Many thanks in advance!

czosnekltd, 2020-10-24:
I had the same issue with KLIPPER/MKSRumba32 and USB. Have you tried to connect via UART?

Bernouillle, 2020-10-26:
@czosnekltd i haven't tried it yet. Can you tell me how i set up the UART connection between the Pi and the MKS Rumba32? Do i have to change something in the configuration file?

czosnekltd, 2020-10-27:
```

  │ │                   [*] Enable extra low-level configuration options                                          │ │
  │ │                       Micro-controller Architecture (STMicroelectronics STM32)  --->                        │ │
  │ │                       Processor model (STM32F446)  --->                                                     │ │
  │ │                       Clock Reference (12 MHz crystal)  --->                                                │ │
  │ │                   [ ] Use USB for communication (instead of serial)                                         │ │
  │ │                   [ ] Use CAN for communication (instead of serial)                                         │ │
  │ │                       **Serial Port (USART1)  ---**>                                                            │ │
  │ │                   (250000) Baud rate for serial port                                                        │ │
  │ │                   [ ] Specify a custom step pulse duration                                                  │ │
  │ │                   ()  GPIO pins to set at micro-controller startup                                          │ │
  │ │
```
In section [MCU] in my case in RPI4:
```
[mcu]
serial: /dev/ttyS0
baud: 250000
restart_method: command
```

Bernouillle, 2020-10-28:
Thanks a lot for your help so far, @czosnekltd! I really appreciate it. I still have one question left. Which pins do i use for the UART connection on the RUMBA32? Are the TX/RX pins of the AUX connector the correct ones? And do i need a GND pin as well?

czosnekltd, 2020-10-28:
I joined:
AUX-1/AUX_TX => RPI/GPIO_15(RXT)
AUX-1/AUX_RX => RPI/GPIO_14(TXT)
AUX-1/GND => RPI/GPIO_GND
The AUX-1 / AUXU_TX / RX outputs differ from EXP3 / USART1_TX / RX in that they are protected with additional resistors, so I think that in principle EXP-3 / USART1_TX / RX can also be connected.
But as I wrote at the beginning, I used pins on the AUX-port for safety.

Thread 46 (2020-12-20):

Sensorless homing fails when Bltouch is connected

McPrince96, 2020-12-20:
Hi,

I've started upgrading my 3d printer a few months back with a new Rumba32 and TMC2130 stepper drivers. Last week i added a BlTouch and did a Marlin update (reconfigured the files).

After testing it, i discovered that my motors keep running after smashing into the sides.
When i disconnect the BlTouch everything works great. I don't even change something, i just disconnect the power and pwm wires.

I have a rumba32 v1.0 board but used v1.1 in Marlin and changed `#define SERVO0_PIN` to PD15. This should be a pwm pin in Aux3. The BlTouch deploys and stows so i think that part is correct.

Is the BlTouch causing interference or is the pin already used by something in v1.1? (Althoug that would cause an error when building the firmware i would think?)

McPrince96, 2020-12-23:
After further investigation i discovered that i can keep the BlTouch power connected to the board if i disconnect to endstop wires.
Maybe this'll help more?

Anyone.....

PLEASE....

McPrince96, 2020-12-30:
Found it.

Disabling `#define ENDSTOP_INTERRUPTS_FEATURE` and `#define ENDSTOP_NOISE_THRESHOLD 2` worked for me.

Closed 2020-12-30.

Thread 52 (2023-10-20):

RUMBA32 Aus3D V1.0 Not appearing under devices in boot mode

alanamer, 2023-10-20:
Hello,

I am trying to upload Marlin to an AUS3D RUMBA32 V1.00 using PlatformIO in Visual Studio Code on a Mac. When the board is not in boot mode, I can see it under devices "RUMBA32_F446VE CDC in FS Mode," however, once it enters boot mode, it is no longer findable. I have tried adding the 100K resistor recommended here[https://github.com/Aus3D/RUMBA32/issues/34]() but that did not resolve the issue. I am entering boot mode by holding boot and then pressing reset, then releasing. There is one flash and then the LED turns off.

Right now, if I try to upload when the board is not showing up, I receive this error: *** [.pio/build/rumba32_f446ve/firmware.bin] Error -6.

This is my platformio.ini configuration:
[env:rumba32_f446ve]
platform = ststm32
board = rumba32_f446ve
framework = arduino
upload_protocol = dfu

I would really appreciate any ideas on how to solve this! Thank you!

alanamer, 2023-10-23:
So I got the firmware to upload through platform ino, but now there is no LED on the board and I am unable to find it as a device in either Pronterface or studio code

coolcheat, 2024-01-01:
I'm using the stlink method, which is a lot more reliant as well as being faster.

You can see here:
https://github.com/Aus3D/RUMBA32/issues/44

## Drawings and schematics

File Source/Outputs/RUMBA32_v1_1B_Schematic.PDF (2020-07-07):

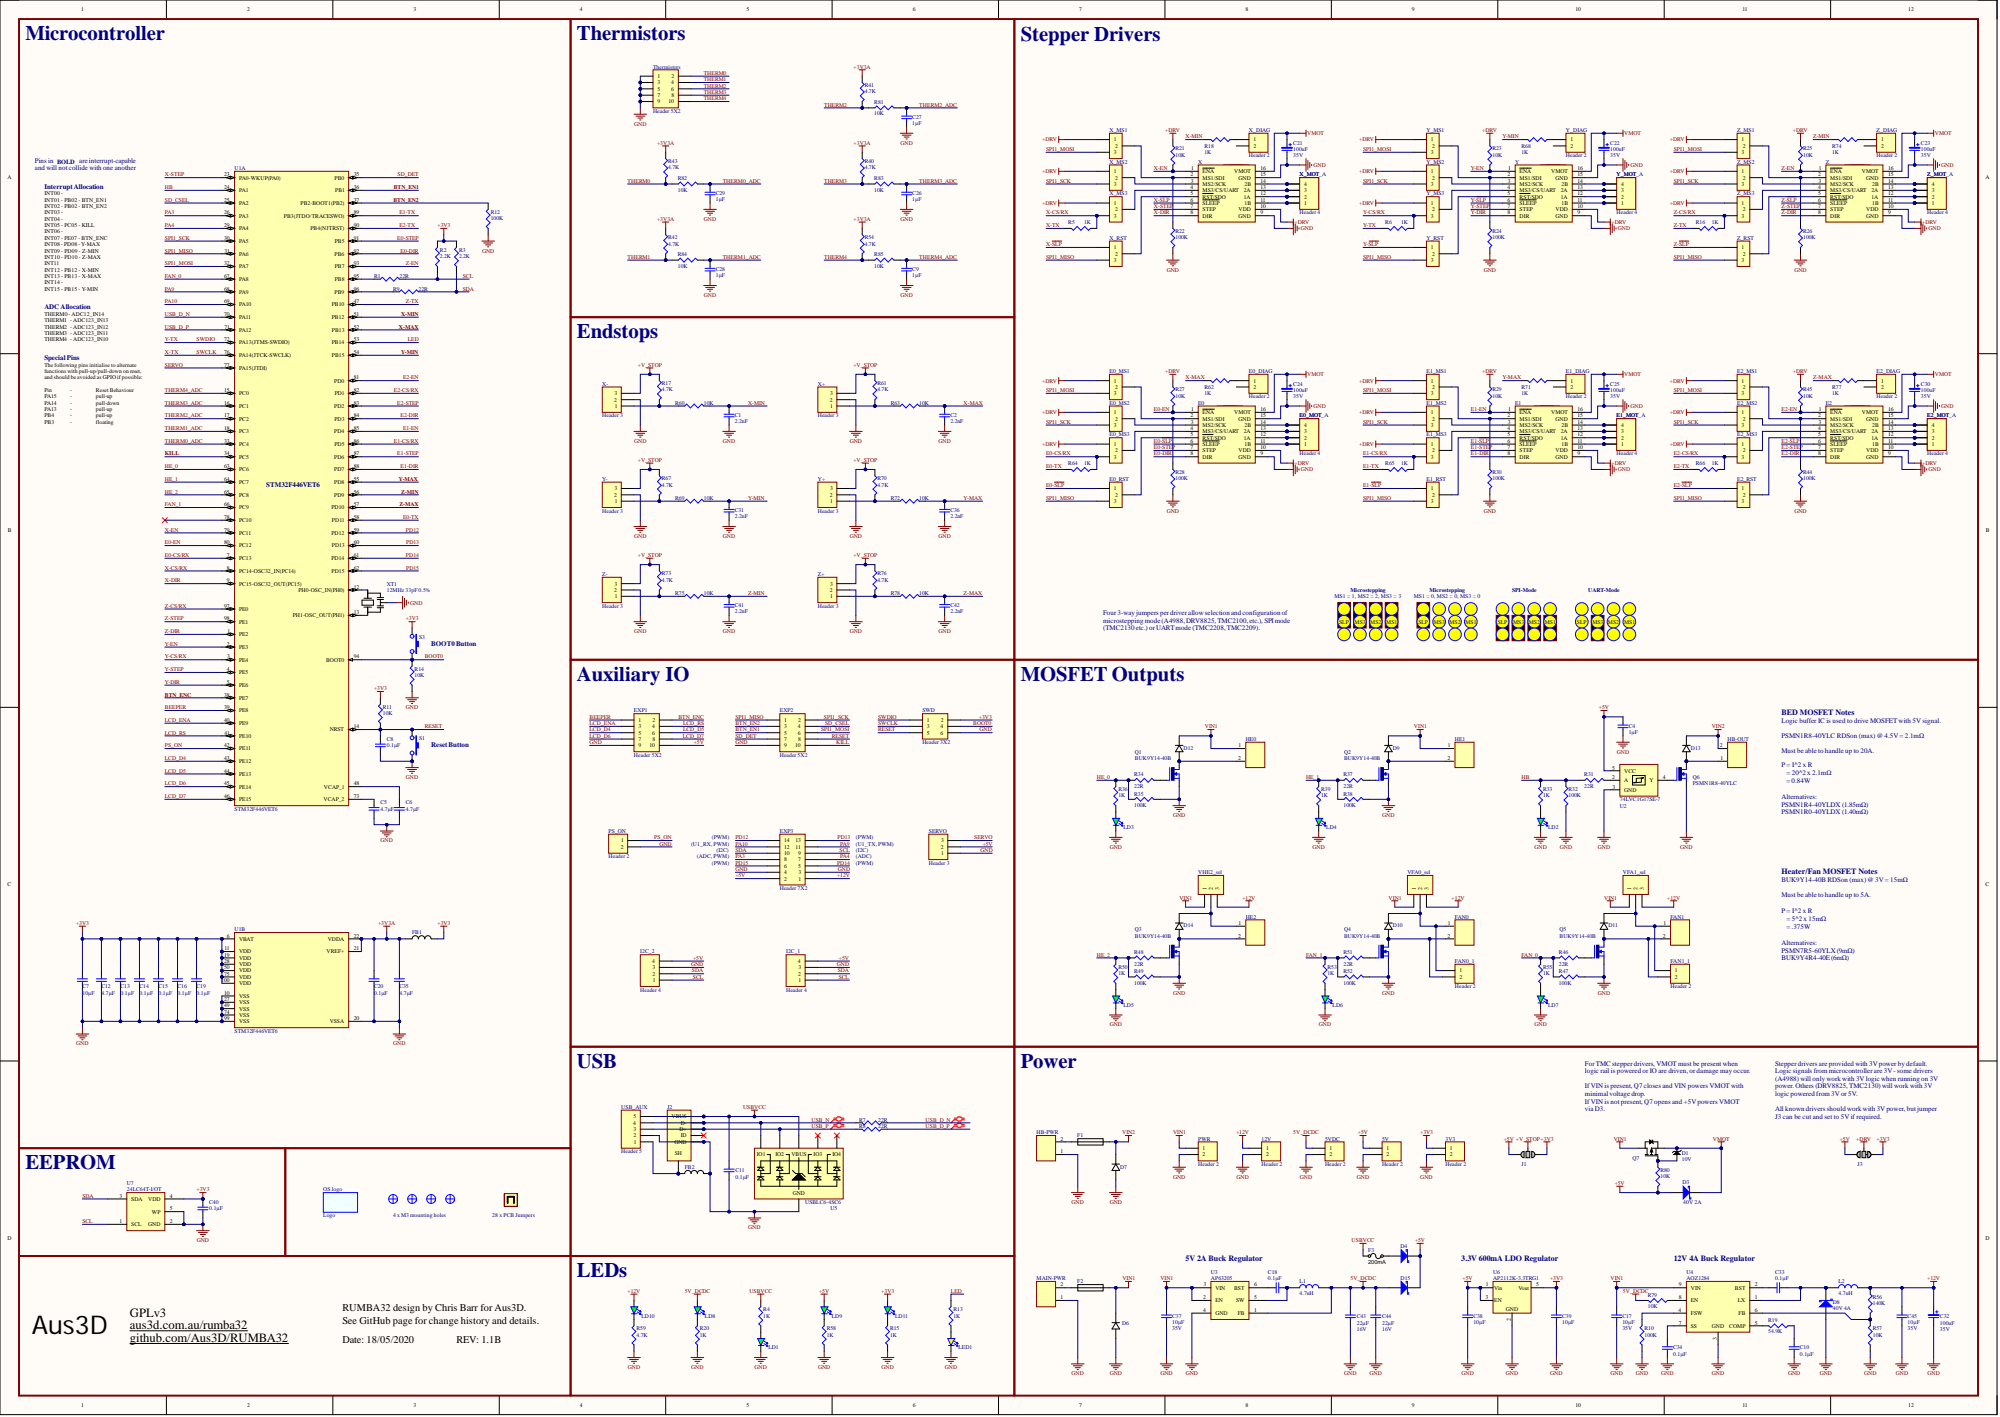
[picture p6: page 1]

Pins in BOLD are interrupt-capable and will not collide with one another

Special Pins
The following pins initialise to alternate
functions with pull-up/pull-down on reset,
and should be avoided as GPIO if possible:

Four 3-way jumpers per driver allow selection and configuration of
microstepping mode (A4988, DRV8825, TMC2100, etc.), SPI mode
(TMC2130 etc.) or UARTmode (TMC2208, TMC2209).

BED MOSFET Notes
Logic buffer IC is used to drive MOSFET with 5V signal.

Must be able to handle up to 20A.

Heater/Fan MOSFET Notes
BUK9Y14-40B RDSon (max) @ 3V = 15mΩ

Must be able to handle up to 5A.

For TMC stepper drivers, VMOT must be present when
logic rail is powered or IO are driven, or damage may occur.

Stepper drivers are provided with 3V power by default.
Logic signals from microcontroller are 3V - some drivers
(A4988) will only work with 3V logic when running on 3V
power. Others (DRV8825, TMC2130) will work with 3V
logic powered from 3V or 5V.

If VIN is present, Q7 closes and VIN powers VMOT with
minimal voltage drop.
If VIN is not present, Q7 opens and +5V powers VMOT
via D3.

All known drivers should work with 3V power, but jumper
J3 can be cut and set to 5V if required.

VBUS D-
D+ | | USB_P
ID GND
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

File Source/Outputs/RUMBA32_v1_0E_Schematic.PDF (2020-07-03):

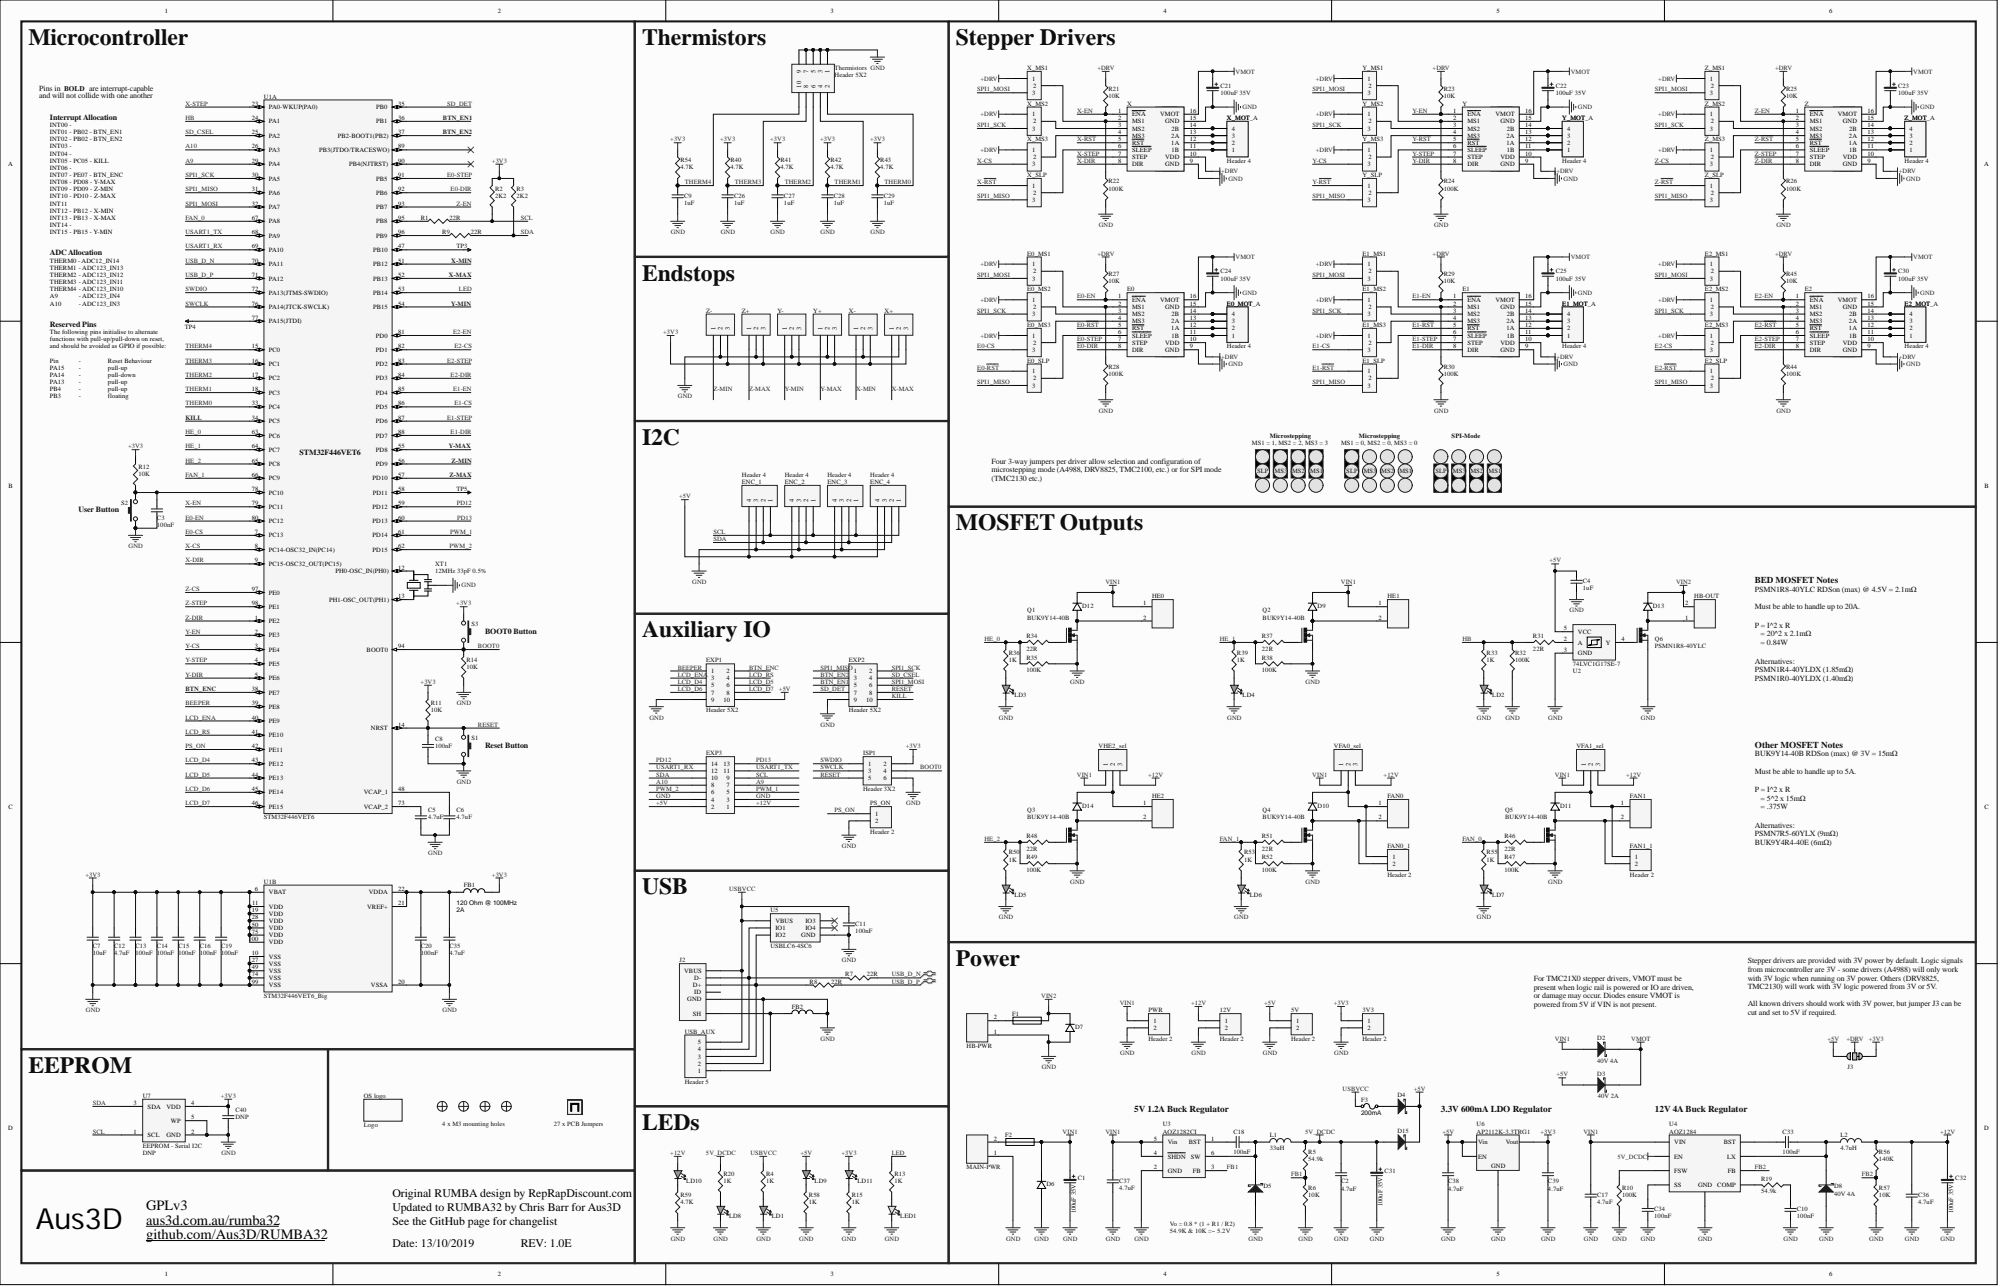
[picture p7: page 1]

Pins in BOLD are interrupt-capable and will not collide with one another

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

Four 3-way jumpers per driver allow selection and configuration of
microstepping mode (A4988, DRV8825, TMC2100, etc.) or for SPI mode
(TMC2130 etc.)

Must be able to handle up to 20A.

Must be able to handle up to 5A.

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

For TMC21X0 stepper drivers, VMOT must be
present when logic rail is powered or IO are driven,
or damage may occur. Diodes ensure VMOT is
powered from 5V if VIN is not present.

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

Original RUMBA design by RepRapDiscount.com

See the GitHub page for changelist
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

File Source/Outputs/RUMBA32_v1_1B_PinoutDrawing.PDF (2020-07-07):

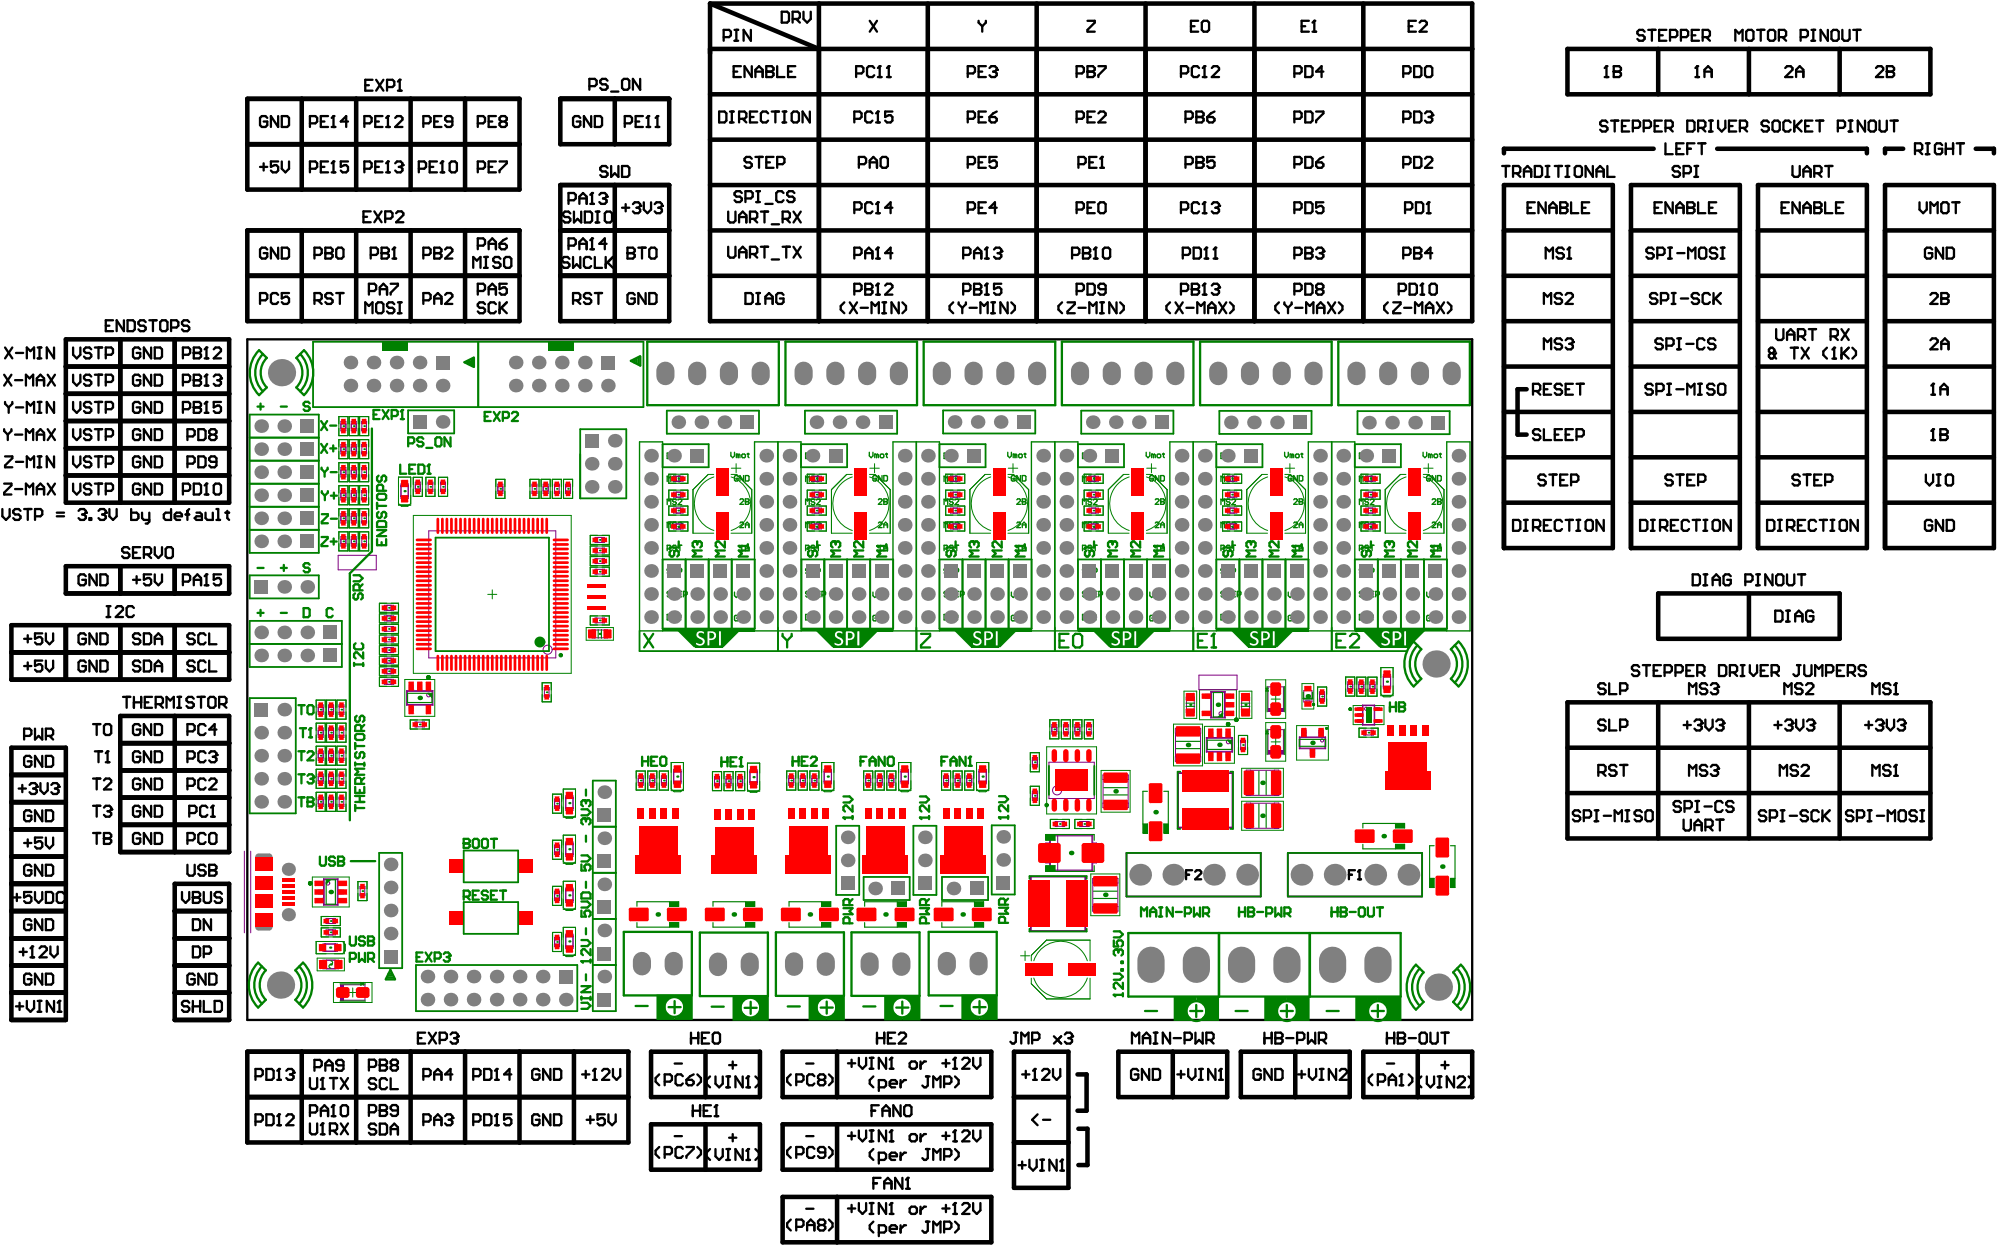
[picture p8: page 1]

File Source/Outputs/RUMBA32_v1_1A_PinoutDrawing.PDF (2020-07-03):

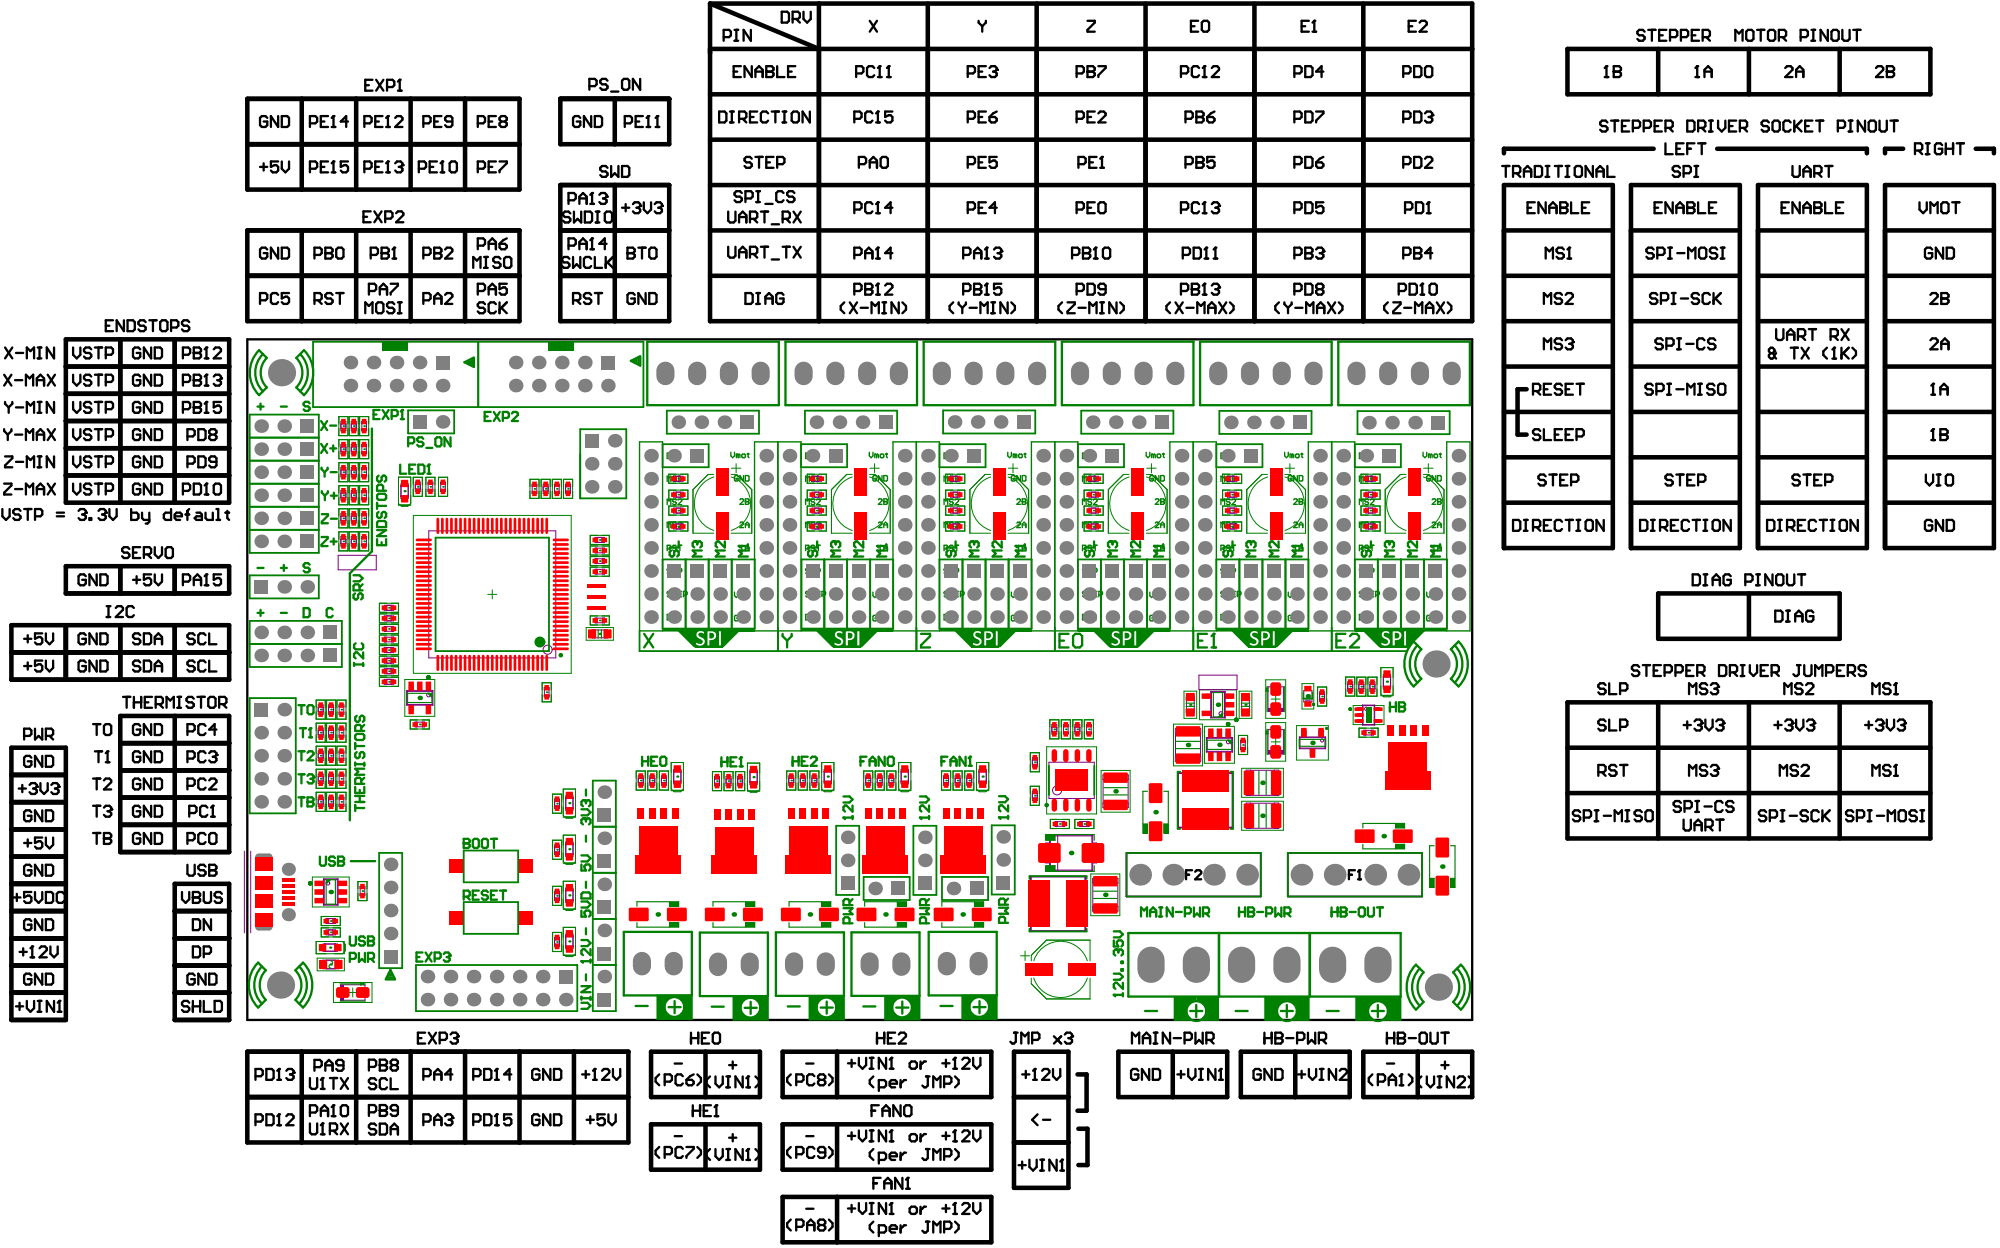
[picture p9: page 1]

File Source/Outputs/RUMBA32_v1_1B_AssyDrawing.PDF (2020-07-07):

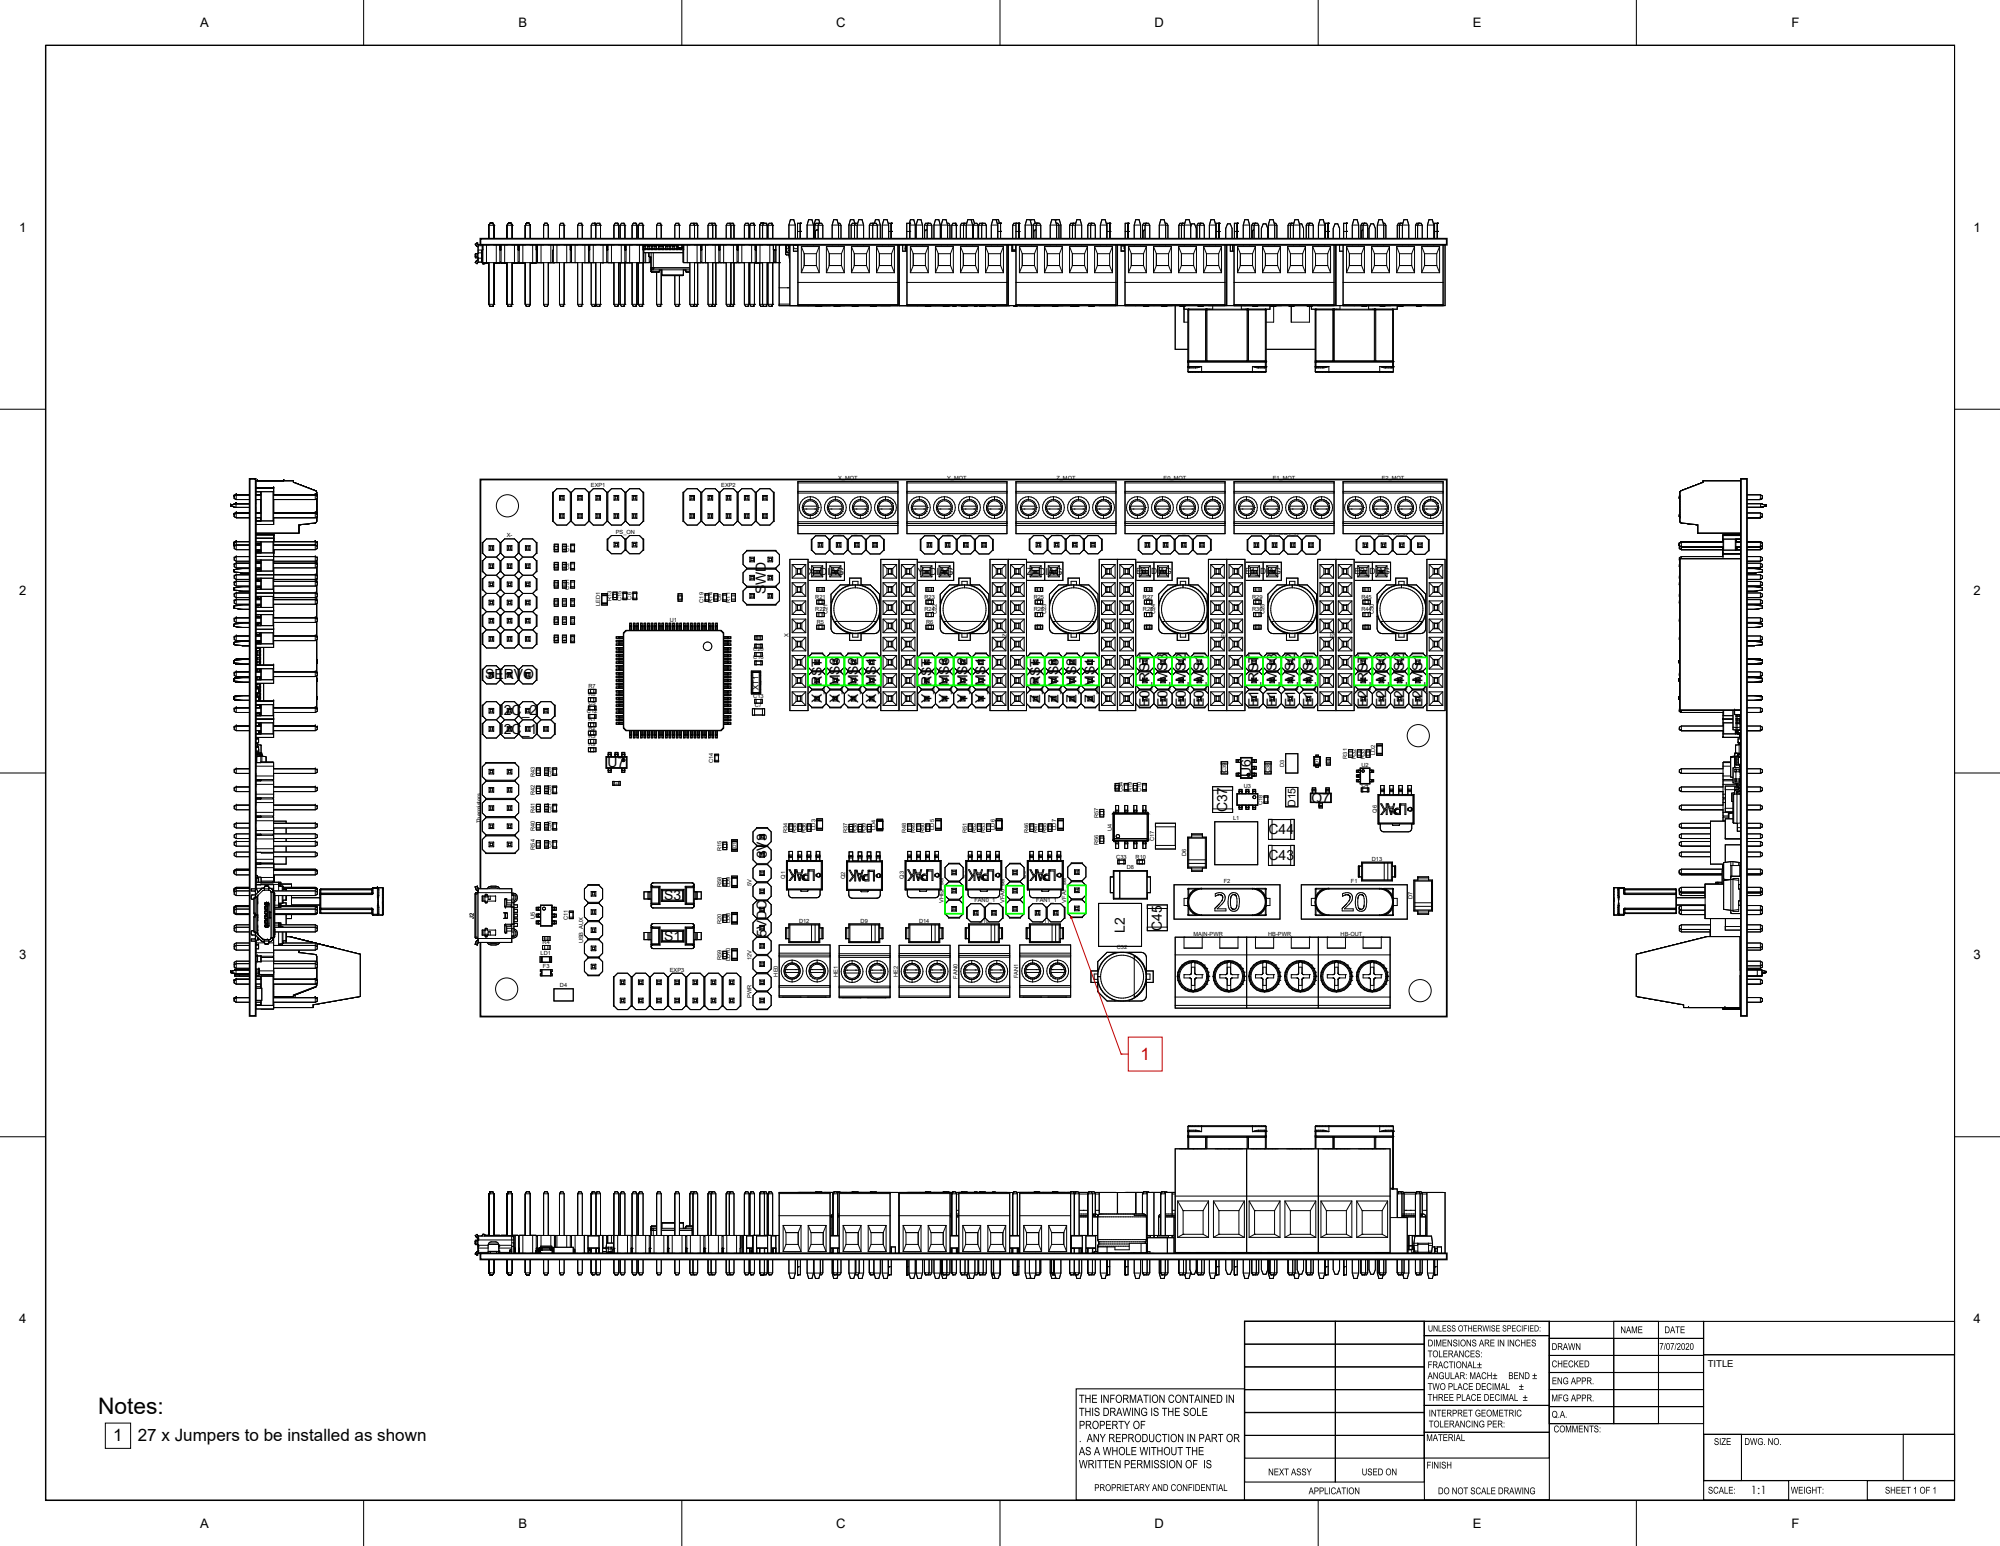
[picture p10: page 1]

Notes:
1 27 x Jumpers to be installed as shown

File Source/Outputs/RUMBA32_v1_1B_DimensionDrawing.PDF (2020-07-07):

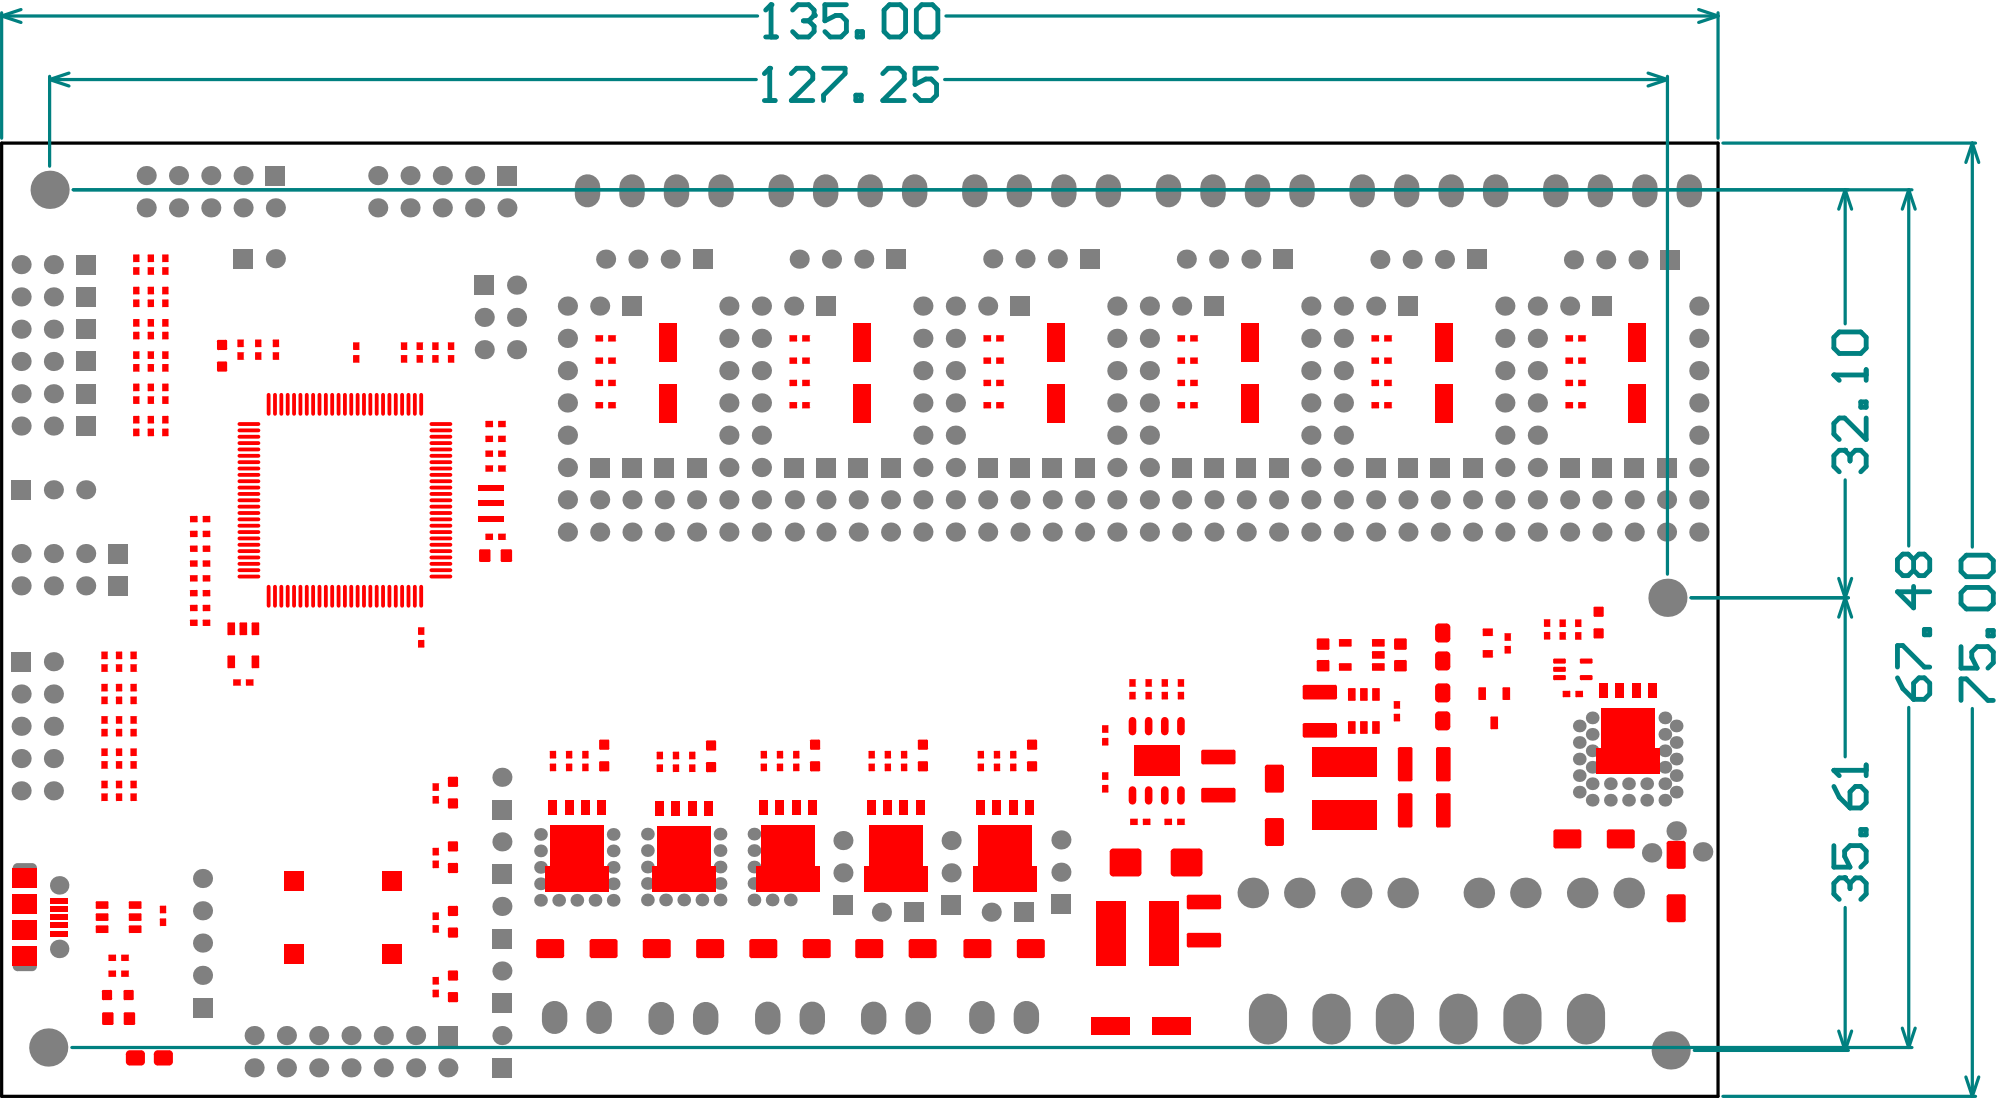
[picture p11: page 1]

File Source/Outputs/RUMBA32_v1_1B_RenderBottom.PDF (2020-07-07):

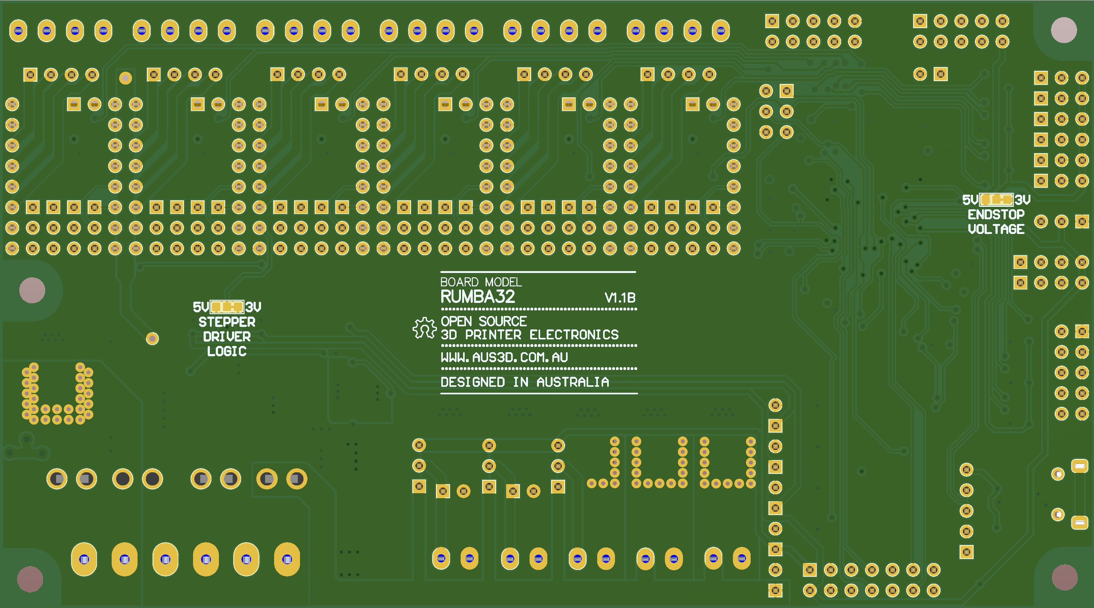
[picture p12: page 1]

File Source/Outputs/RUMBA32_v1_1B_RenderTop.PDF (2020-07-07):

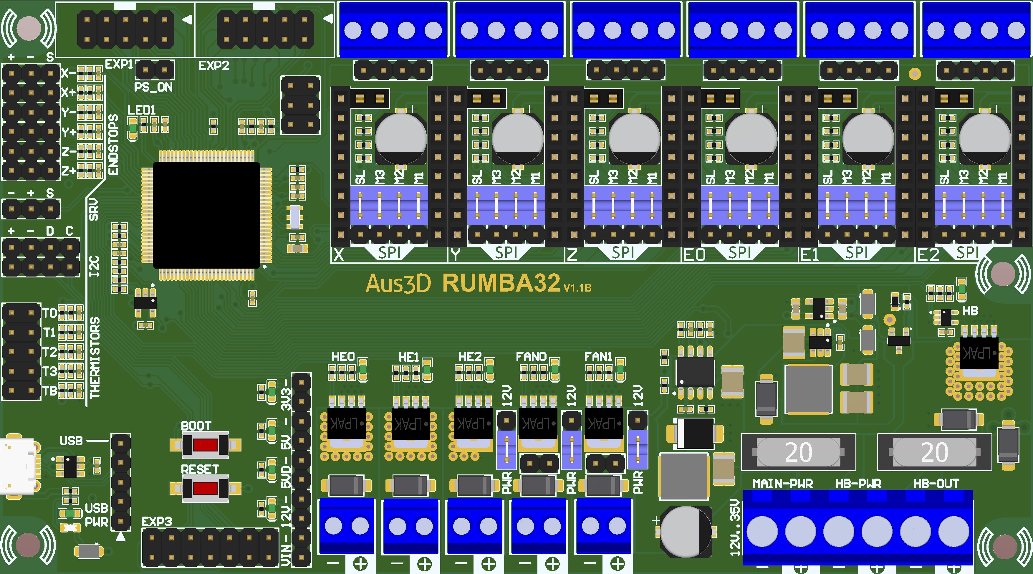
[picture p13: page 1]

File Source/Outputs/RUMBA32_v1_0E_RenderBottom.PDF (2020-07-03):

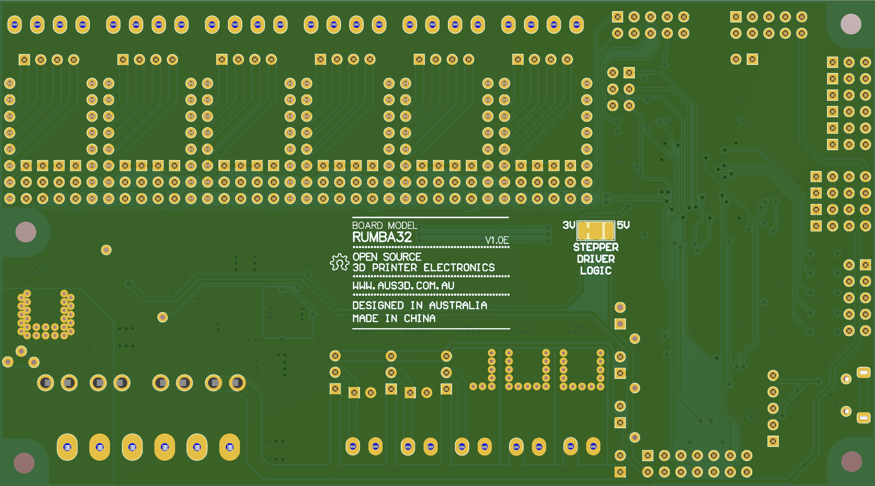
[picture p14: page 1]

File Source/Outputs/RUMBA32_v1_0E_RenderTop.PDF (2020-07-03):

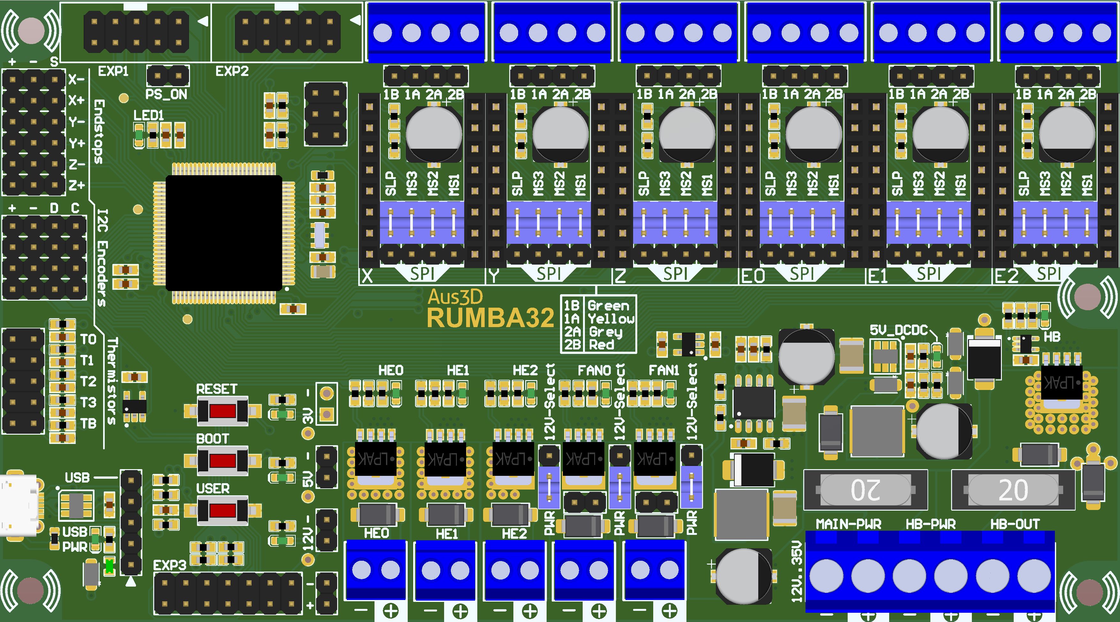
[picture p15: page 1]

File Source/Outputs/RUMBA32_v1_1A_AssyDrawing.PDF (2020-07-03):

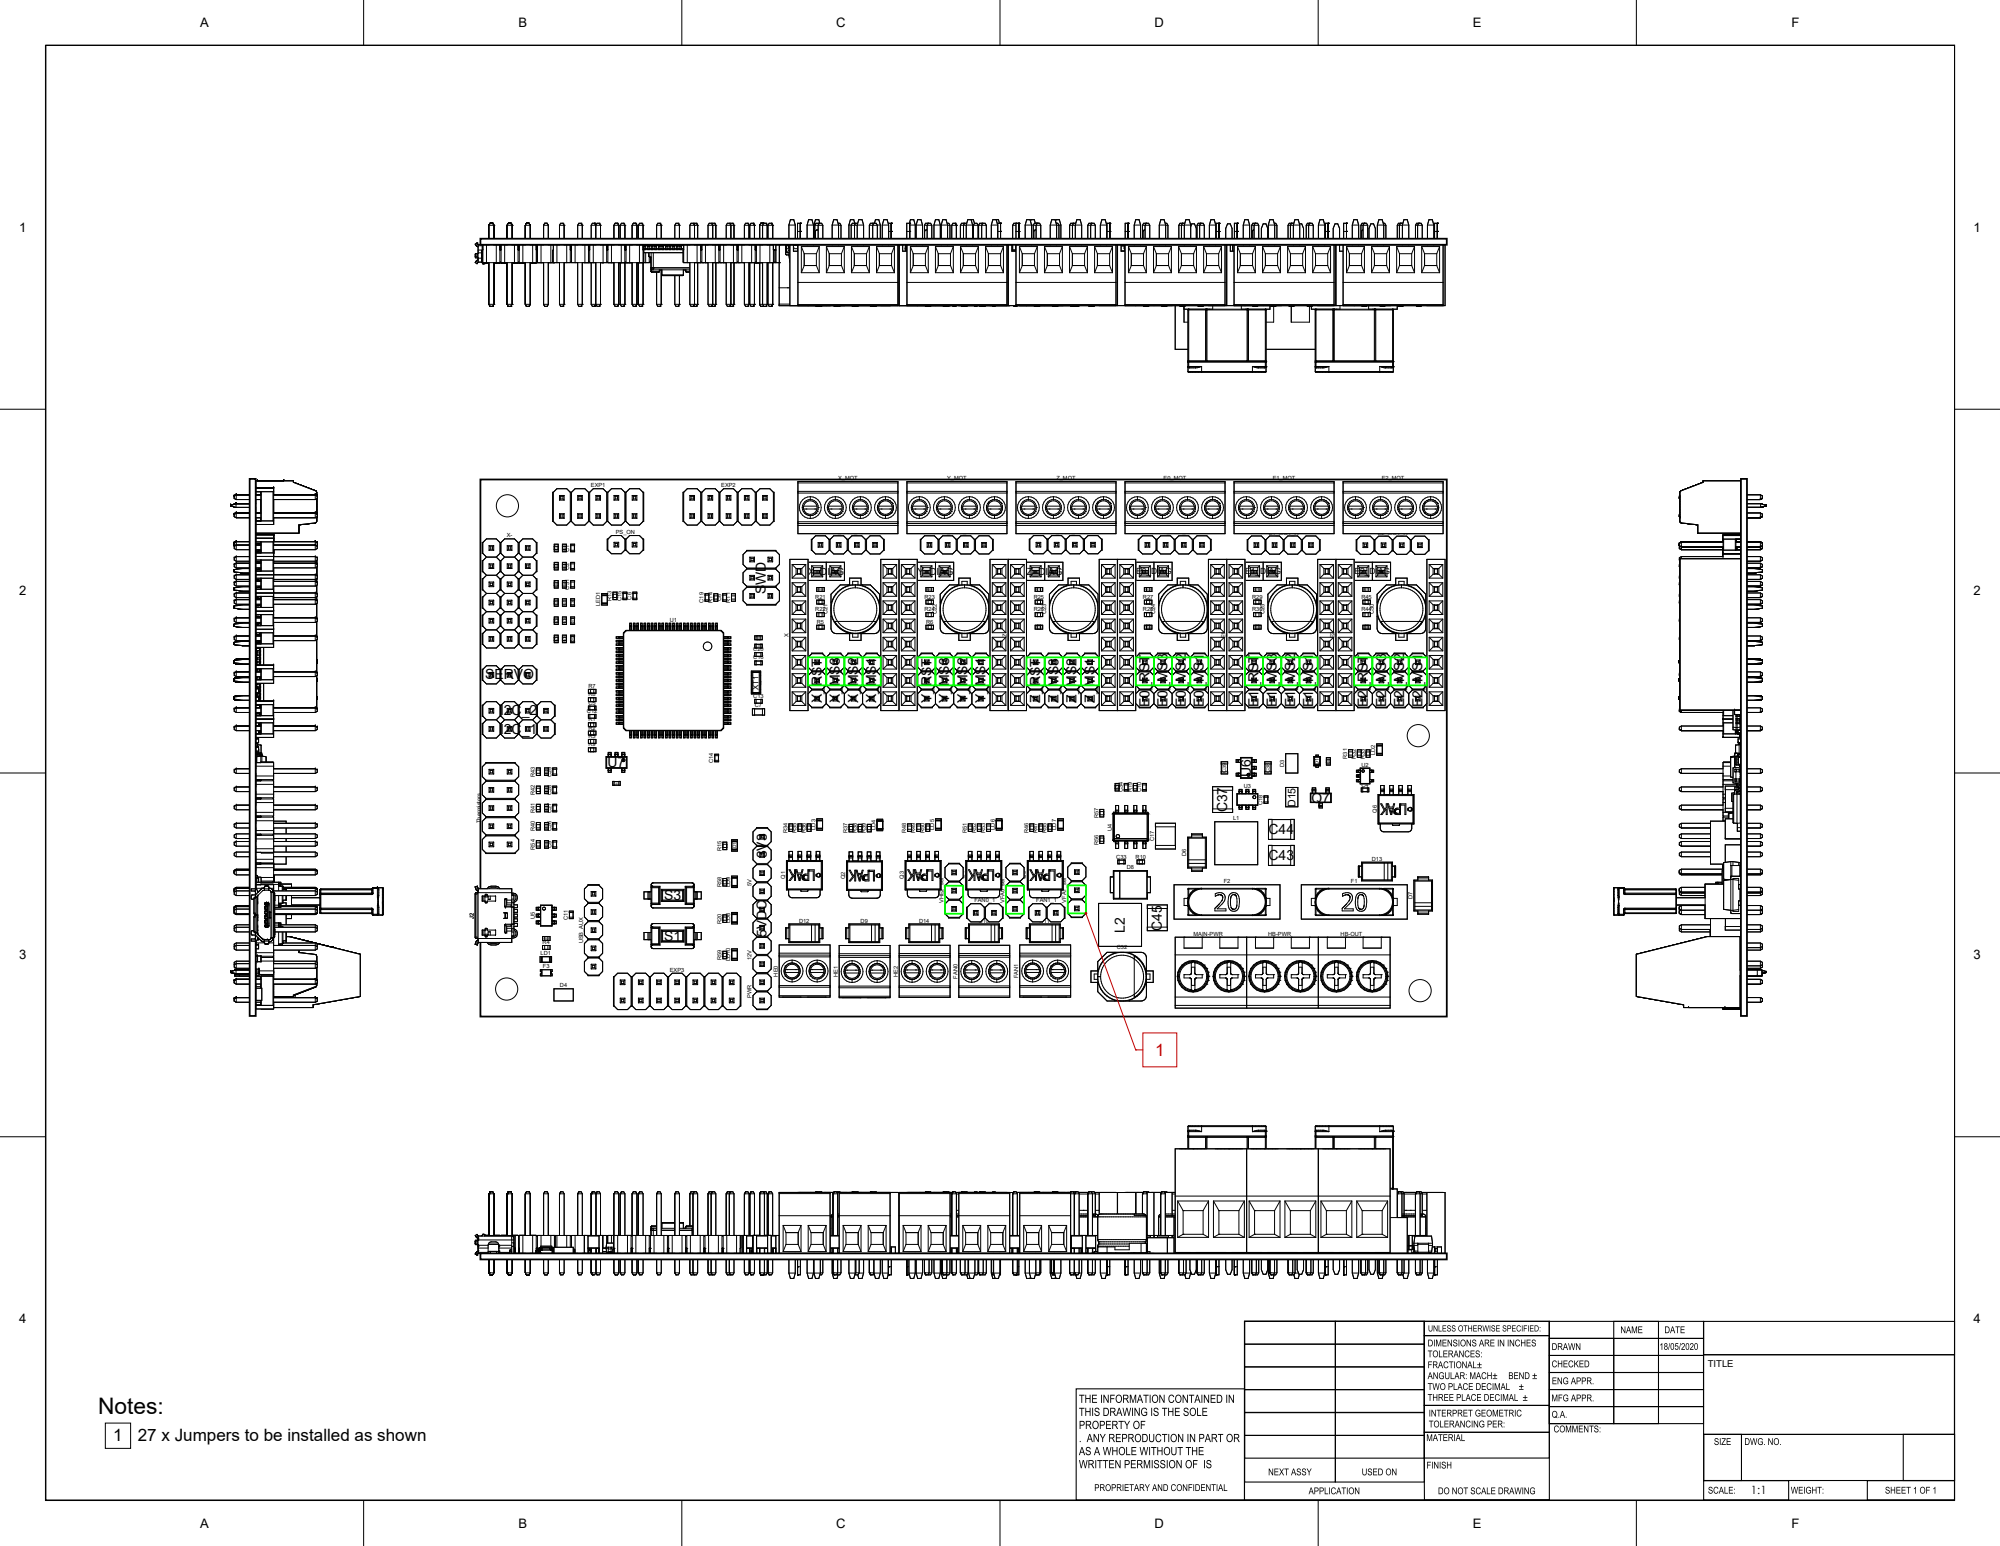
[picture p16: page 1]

Notes:
1 27 x Jumpers to be installed as shown

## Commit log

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2016-05-24 WIP
    BOM partially completed. PTC fuses changed to blade-style fuse holders for > 12V operation. Flyback diodes for MOSFETs added to schematic but not board yet. Need to find better logic-level MOSFETs.
    [RUMBA_V2.SchDoc, RUMBA_v2.PrjPCB, RUMBA_v2.SCHLIB]
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2016-05-25 Tidying Files
    Add images, schematic + BOM in PDF format. Tidy folder structure.
    [Pick Place for RUMBA_V2.csv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]
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2016-07-09 Correct 16U2 DTR Pin
    [RUMBA_plus.PrjPCB, RUMBA_plus.SchDoc]
2016-07-09 Uniform screw holes
    Fix inconsistent sizing on screw holes
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2016-07-27 Change 5V regulator
    Change LT1933 regulator to AOZ1282CI. Higher current rating (1.2A vs 600mA) and easier to source. Feedback resistors to set voltage changed accordingly.
    [RUMBA_V21.PcbLib, RUMBA_plus.SchDoc, RUMBA_plus_BOM.xlsx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]
2016-09-21 Adjust heated bed traces
    Beefing up connection between HB fuse and screw terminal, this was found to be the 'weakest link' in a thermal analysis. It wasn't really a problem, existing trace was easily handling 10A+, but might as well improve it.
2016-09-21 Increase spacing between ISP2 and 5V headers. Distance between EXP3 and 12V header changed to match. Hopefully fixes #2.
2016-09-21 Correct DIP switch orientation
    Stepper driver microstepping DIP switches are 'upside-down' / unintuitive, change orientation.
    [RUMBA_plus.SchDoc]
2016-09-21 Fix D8 Footprint
    Diode D8 was using footprint for MBMR140 instead of MURS320. Previous boards were populated with MBMR140 to suit footprint, potentially limiting regulated 12V output current.
    [RUMBA_plus.SchDoc]
2016-09-21 V1.1 outputs
    Update version number on PCB and schematic to V1.1A
    Update Gerbers
    Update pick and place
    Update Schematic and BOM PDF
    Check Excel BOM correct
    Update Schematic image
    [RUMBA_plus.GBL, RUMBA_plus.GBO, RUMBA_plus.GBS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]
2016-09-22 Correct v1.1 gerbers
    Wrong outline, missing top layer.
    [RUMBA_plus.GBL, RUMBA_plus.GBO, RUMBA_plus.GBS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]
2016-09-26 Rework voltage regulators
    Change inductors to be smaller, higher current ratings
    Change diode D8 to be smaller, higher ratings
    [RUMBA_plus.GBL, RUMBA_plus.GBO, RUMBA_plus.GBS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]
2016-11-07 Improve 5V regulator
    Change diode D5 to DB2W40200L - higher current capacity + smaller + easier footprint
    Improve routing of power and ground, add vias to improve thermal conductivity to ground plane
    [RUMBA_plus.PrjPCB, RUMBA_plus.SchDoc, RUMBA_plus_BOM.xlsx]
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2017-11-01 Fix SMD crystal footprint
    [RUMBA_V21.PcbLib, RUMBA_plus.PrjPCB]
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2017-11-01 Update MOSFETs
    Change heater and fan MOSFETs to BUK9Y21-40E - cheaper, improved gate-capacitance, logic-level, still very good RDSon. No loss of performance or significant heating at heater or fan current levels.
    Leave bed MOSFET as PSMN1R8 for maximum current capability.
    Change MOSFET numbering to make BOM tidier.
    [RUMBA_library.SCHLIB, RUMBA_plus.SchDoc, RUMBA_plus_BOM_1_3_0.xlsx]
2017-11-01 Change diode D8
    D8's forward voltage is the limiting factor in 12V regulator current capability, currently gets uncomfortably hot running 12V 40W heater cartridges. Changing D8 to SSB44-E3, lower forward-voltage tha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
    [RUMBA_library.SCHLIB, RUMBA_plus.SchDoc, RUMBA_plus_BOM_1_3_0.xlsx]
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2018-05-24 Initial v1.4 changes
    Move fuses upward slightly, make room for deeper screw terminals, adjust silkscreen labelling.
    [RUMBA_plus.PrjPCB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]
2018-05-30 Change 16U2 from AU to MU package
    Smaller, better stock availability
    [RUMBA_plus.PrjPCB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]
2018-07-16 Tidying for v1.4
    Updating images
    Removing old files
    [RUMBA_V2.PcbLib, RUMBA_plus.PrjPCB, RUMBA_plus.SchDoc]
2018-07-18 Update dimension image
    Tidy up mounting dimensions on PCB and update image
    [RUMBA_plus.PrjPCB]
2018-08-08 Change to RUMBA32
    Change project/file names, remove output files
    [Assembly Testpoint Report for RUMBA_plus.csv, RUMBA32.PrjPCB, RUMBA32.SchDoc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]
2018-08-08 Initial microcontroller changes
    Remove 2560 and 16u2, add F446 in similar pinout to PicoPrint.
    [RUMBA32.SchDoc]
2018-08-08 Update LEDs
    Add LED for 3V3 rail.
    Group LEDs together in dedicated block.
    [RUMBA32.SchDoc]
2018-08-09 Stepper Driver Work
    Replace DIP switches with jumpers.
    Change stepper driver sockets to support TMC2130 in SPI mode via config jumpers.
    Add separate power rail for motors, use diodes to ensure rail is powered by 5V if VIN is not present - protects TMC21x0 from damage if 3V is present or GPIO are driven.
    [RUMBA32.SchDoc]
2018-08-10 Update BOM
    Update BOM to more consistent naming
    Change 0402 parts to 0603
    Simplify resistors / capacitors, minimise line items
    Start MOSFET work
    [RUMBA32.PrjPCB, RUMBA32.SchDoc]
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2018-08-17 Routing Done
    Routing work finished and PCB tentatively ready for prototyping. Several schematic changes - mostly microcontroller pinout, but also changes to 12V regulator.
    [RUMBA32.PrjPCB, RUMBA32.SchDoc]
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2018-08-17 Update README.md
    Fix schematic image
2018-08-23 Update to v1.0B
    Change bed MOSFET to BUK9Y4R4-40E
    Remove jumper to select bed MOSFET driver voltage source, hardwired to 5V (BUK9Y4R4-40E has +/- 10V as maximum VGS, so 12V could be damaging).
    [RUMBA32.PrjPCB, RUMBA32.SchDoc, RUMBA32_v1_0B_BOM.xlsx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]
2018-10-08 v1.0B fixes
    - Remap HEATER_BED_PIN to PWM capable pin
    - Remap FAN_PIN to PWM capable pin
    - Tidy labeling of stepper driver jumpers
    - Change stepper driver voltage jumper to default to 3V (as per schematic)
    - Add back in MOSFET driver voltage select, default to 5V
    - Move 5V regulator voltage sense trace away from noise source under regulator IC
    - Add pads for optional I2C EEPROM
    - Add SMD test points for three unused STM32F4 pins
    - General tidying of schematic and PCB routing
    [RUMBA32.PrjPCB, RUMBA32.SchDoc]
2018-10-09 Add THERM0 to ADC allocation list in schematic
    [RUMBA32.SchDoc]
2018-10-09 Change Bed MOSFET
    Change to SiSS10DN (PowerPAK 1212-8S package). Advantages compared to previous MOSFET:
    - Lower RDSon at 4.5V: 3.0/3.6 vs 3.7/4.4
    - Vgs can tolerate +20V, not just +10V (so 12V drive is an option)
    [RUMBA32.SchDoc]
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2019-01-08 Update board photo
    Replace RUMBA+ photo with RUMBA32 V1.0C.
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2019-05-29 Tidy BOM
    Clean up part descriptions in Altium and regenerate BOM
    [RUMBA32.SchDoc, RUMBA32_v1_0D_BOM.xlsx]
2019-05-29 Change bed MOSFET
    Change bed MOSFET to same part as RUMBA+ (PSMN1R8).
    [RUMBA32.SchDoc]
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2019-10-13 Fix PD12 & PD13 on schematic
    Pins on EXP3 were wrongly labelled
    [RUMBA32.SchDoc]
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2019-10-16 Fix stepper driver SPI pinout
    Swap stepper driver SLP and RST pins so SPI MISO can be connected correctly.
    [RUMBA32.SchDoc]
2020-04-15 Schematic updates
    Working towards next version:
    - Add support for TMC2208/2209 UART mode
    - Add support for TMC StallGuard DIAG pin
    - Add RC filters and pullups to endstop signals
    - Add servo header
    - Improve 5V power supply (change regulator to AP63205, 2A synchronous buck regulator)
    - Remove 2 x I2C headers (leaving 2) to make room
    - Add jumper for selecting endstop voltage
    - Tidy schematic
    [RUMBA32.SchDoc]
2020-04-28 Further schematic updates
    - Change endstop VDD select to solder jumper (jumper pins take up too much space, unlikely to be used)
    - Replace Stepper Driver VMOT diode with P-FET (reduces voltage drop from VIN to VMOT)
    - Change stepper diag header to female part
    - Tidying
    [RUMBA32.SchDoc]
2020-04-30 Further schematic updates
    Change majority of passives to 0402 size.
    Tidying.
    [RUMBA32.SchDoc]
2020-05-03 Further schematic updates
    - Add series resistor to thermistor inputs
    - Change schematic sheet size to A1
    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
    [RUMBA32.SchDoc]
2020-05-07 Further schematic updates
    Modify endstop circuitry:
    - Change to 10K series resistor
    - Move pullup before RC filter
    [RUMBA32.SchDoc]
2020-05-12 Further schematic updates
    - Change ferrite beads to 0402 package
    - Change 3-way solder jumper footprint to smaller layout
    - Rotate fuse F2 so both fuses have same orientation on PCB
    [RUMBA32.SchDoc]
2020-05-15 Routing updates
    Change 0603 fuse footprint to match other 0603 footprints.
    Change LED/resistor ordering to make routing consistent.
    Nearly finished with PCB routing
    [RUMBA32.SchDoc]
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2020-05-18 Increment version to 1.1A
    Update schematic, PCB and project file with new version.
    Touch up silkscreen on PCB.
    [RUMBA32.PrjPCB, RUMBA32.SchDoc]
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2020-05-18 Finalise BOM
    Update part numbers for BOM as appropriate
    [RUMBA32.SchDoc]
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2020-06-24 Tidy schematic
    Rename pins on AUX3, change some labeling etc. Regenerate images.
    [RUMBA32.SchDoc]
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2020-07-07 Update schematic image
    FIx schematic image to be V1.1B.
2020-07-08 Tidy v1.1B BOM
    No change to items in BOM, just tidying columns to match previous + updating Outjob accordingly.
    [RUMBA32_v1_1B_BOM.xlsx]

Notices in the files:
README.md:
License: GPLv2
